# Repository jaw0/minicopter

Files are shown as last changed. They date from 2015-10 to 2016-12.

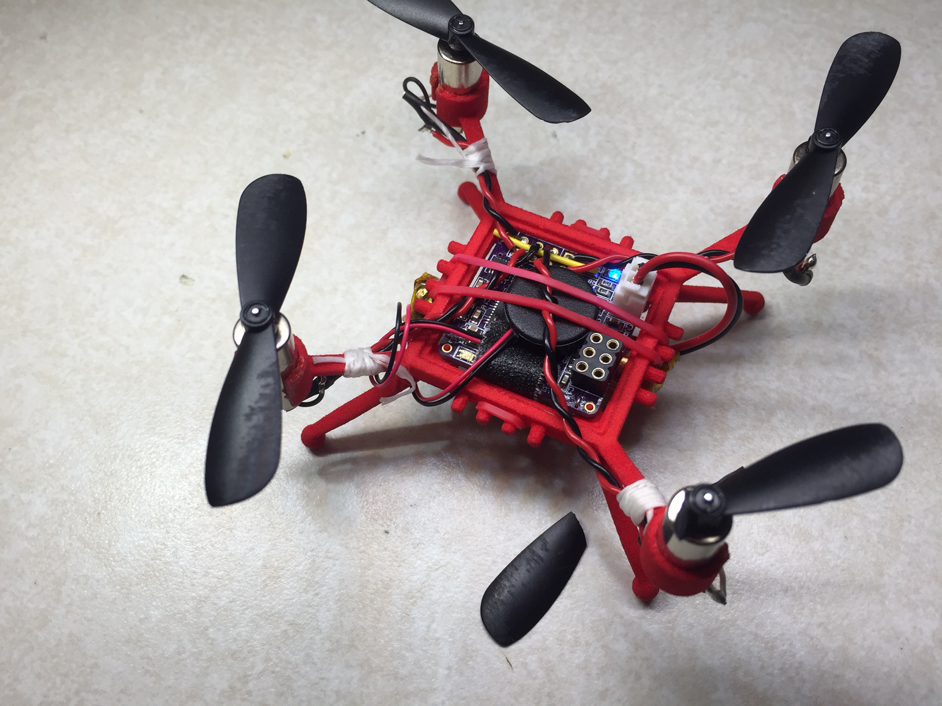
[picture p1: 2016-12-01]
img/IMG_0938.JPG

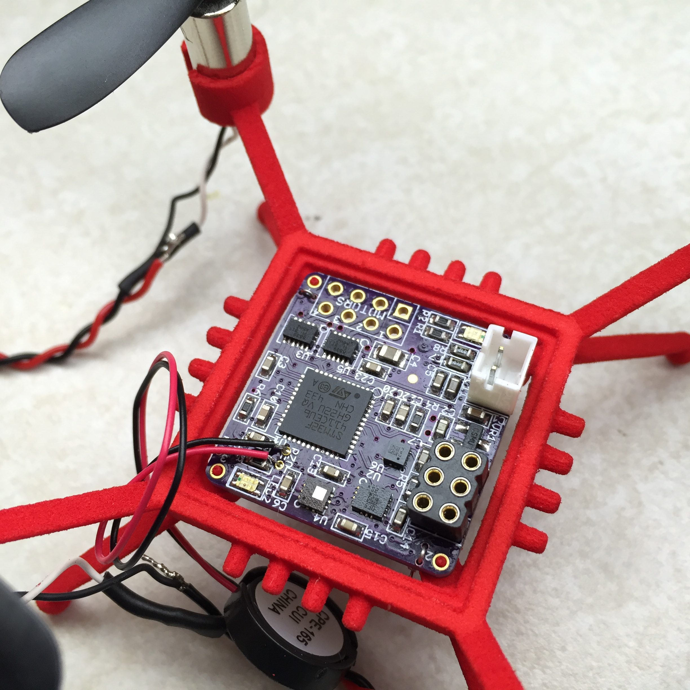
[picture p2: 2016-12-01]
img/IMG_0904.JPG

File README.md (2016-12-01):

teeny-tiny autonomous quadcopter flying machine

* 25mm square (smaller than one inch!)

* STM32F4 - ARM Cortex-M4

* 10 DOF IMU
  * accelerometer
  * gyro
  * magnetometer
  * barometer

* 3D printed frame

* buggy, poorly performing software

* see also: [hackaday.io](https://hackaday.io/project/7947-quadcopter-in-one-inch)

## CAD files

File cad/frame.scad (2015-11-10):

// Copyright (c) 2015
// Author: Jeff Weisberg <jaw @ tcp4me.com>
// Created: 2015-Oct-04 22:32 (EDT)
// Function: frame for mini-copter


show_env   = 0;

pcb_x      = 25.0;
pcb_y      = 25.0;
pcb_z      =  1.6;

peg_pos    = 1.25;	// in from corner
prop_x     = 56.0;	// prop diam plus margin
mot_z      = 10.0; 	// ht of center of motor
motor_phi  = 5.0;	// slight dihedral
motor_diam = 7;


//################################################################

mot_pos = (prop_x - pcb_x) / 2;
mot_armang = atan( (mot_z + 2) / (mot_pos + peg_pos) / sqrt(2) );

$fn = 64;
$fa = .5;
$fs = 0.05;

//################################################################

module vcyl(x,y,z,diam1, diam2, len){
    translate([x,y,z])
        cylinder(r1=diam1/2, r2=diam2/2, h=len);
}

module hcyl(x,y,z,diam1, diam2, len){
    translate([x,y,z])
        rotate([0,90,0])
            cylinder(r1=diam1/2, r2=diam2/2, h=len);
}

module box(x,y,z, dx,dy,dz){
    translate([x, y, z]) cube([dx, dy, dz]);
}


module proparm(){

    // board support+attach
    translate([ (pcb_x/2-peg_pos)*sqrt(2), 0, 0]) rotate([0,0,45]){
        vcyl(0,0,-4, 3.5, 3.5,4);
        // slightly tapered pins
        vcyl(0,0,-.1, 1.0, 0.85, 2.1);
        box(-3.5,-.5,-1.5, 4,1,1.5);
        box( -.5,-.5,-1.5, 1,4,1.5);

    }

    // legs
    translate([ (pcb_x/2-peg_pos)*sqrt(2), 0, -3.0]) rotate([0,30,0]){

        intersection(){
            union(){
                box(0,-1.5,2.0, 25, 3, 1);
                rotate([0,-3,0]) box(0,-.5,0, 25, 1, 3);
            }
            box(0,-1.5,-1, 25, 3, 4);
            hcyl(0,0,2.5, 5.3,2.25, 25);
        }
        translate([25,0,1.25]) sphere(2.0);
    }

    difference(){
        union(){
            // motor arms
            intersection(){
                translate([ (pcb_x/2-peg_pos)*sqrt(2), 0, -2.0]) rotate([0,-mot_armang,0]) {
                    box(0, -1.5, 0,   (mot_pos+peg_pos)*sqrt(2) / cos(mot_armang), 3.0,1 );
                    box(0,-.5,  -2, (mot_pos+peg_pos)*sqrt(2) / cos(mot_armang), 1,3.0 );
                }
                // clean up the bottom
                box(-5,-5,-4, 60,60,60);
            }
            // motor mounts
            translate([prop_x/2 * sqrt(2),0, mot_z]) rotate([0,-motor_phi,0]){
                vcyl(0,0,-3.5, motor_diam+2, motor_diam+2, 6.5 );

                // prop
                if( show_env ) color([.75,0,.75,1]) vcyl(0,0,5, 45, 45, 5);
            }

        }
        union(){
            // hole for motor
            translate([prop_x/2 * sqrt(2),0, mot_z]) rotate([0,-motor_phi,0]){
                vcyl(0,0,-5, motor_diam-.5, motor_diam-.5, 9 );
                rotate([0,0,90]) box(motor_diam/2-2, -.5,-5, 5,1,9);
            }
        }
    }
}

module cage(){
    // outer box
    difference(){
        union(){
            box( 28/2+.5, -28/2-2, -2.0, 2.0, 28+4, 4.0);
            box( 28/2-.5,  -28/2-2, -1.0, 2.0, 28+4, 2.0);
        }
        // clean up/bevel the corners
        union(){
            for(a = [-45, 45]){
                rotate([0,0,a])
                    translate([ (pcb_x/2-peg_pos)*sqrt(2), 0, 0])
                        rotate([0,-mot_armang,0])
                            box(-2,-4,-6.1,  8,8,2);
            }
        }
    }
    // rubber band attachment pegs
    hcyl(28/2+.5, -6, 0,  2,2,5);
    hcyl(28/2+.5,  6, 0,  2,2,5);
    hcyl(28/2+.5, -2, 0,  2,2,5);
    hcyl(28/2+.5,  2, 0,  2,2,5);

}


// ################################################################

if( show_env ) color([.75,0,.75, 1]) box(-pcb_x/2, -pcb_y/2, 0, pcb_x, pcb_y, pcb_z);

for( angle = [ 0 : 90 : 270 ] ){
    rotate([0,0,45+angle]) proparm();

    // outer cage
    rotate([0,0,angle]) translate([0,0,.4]) cage();

}

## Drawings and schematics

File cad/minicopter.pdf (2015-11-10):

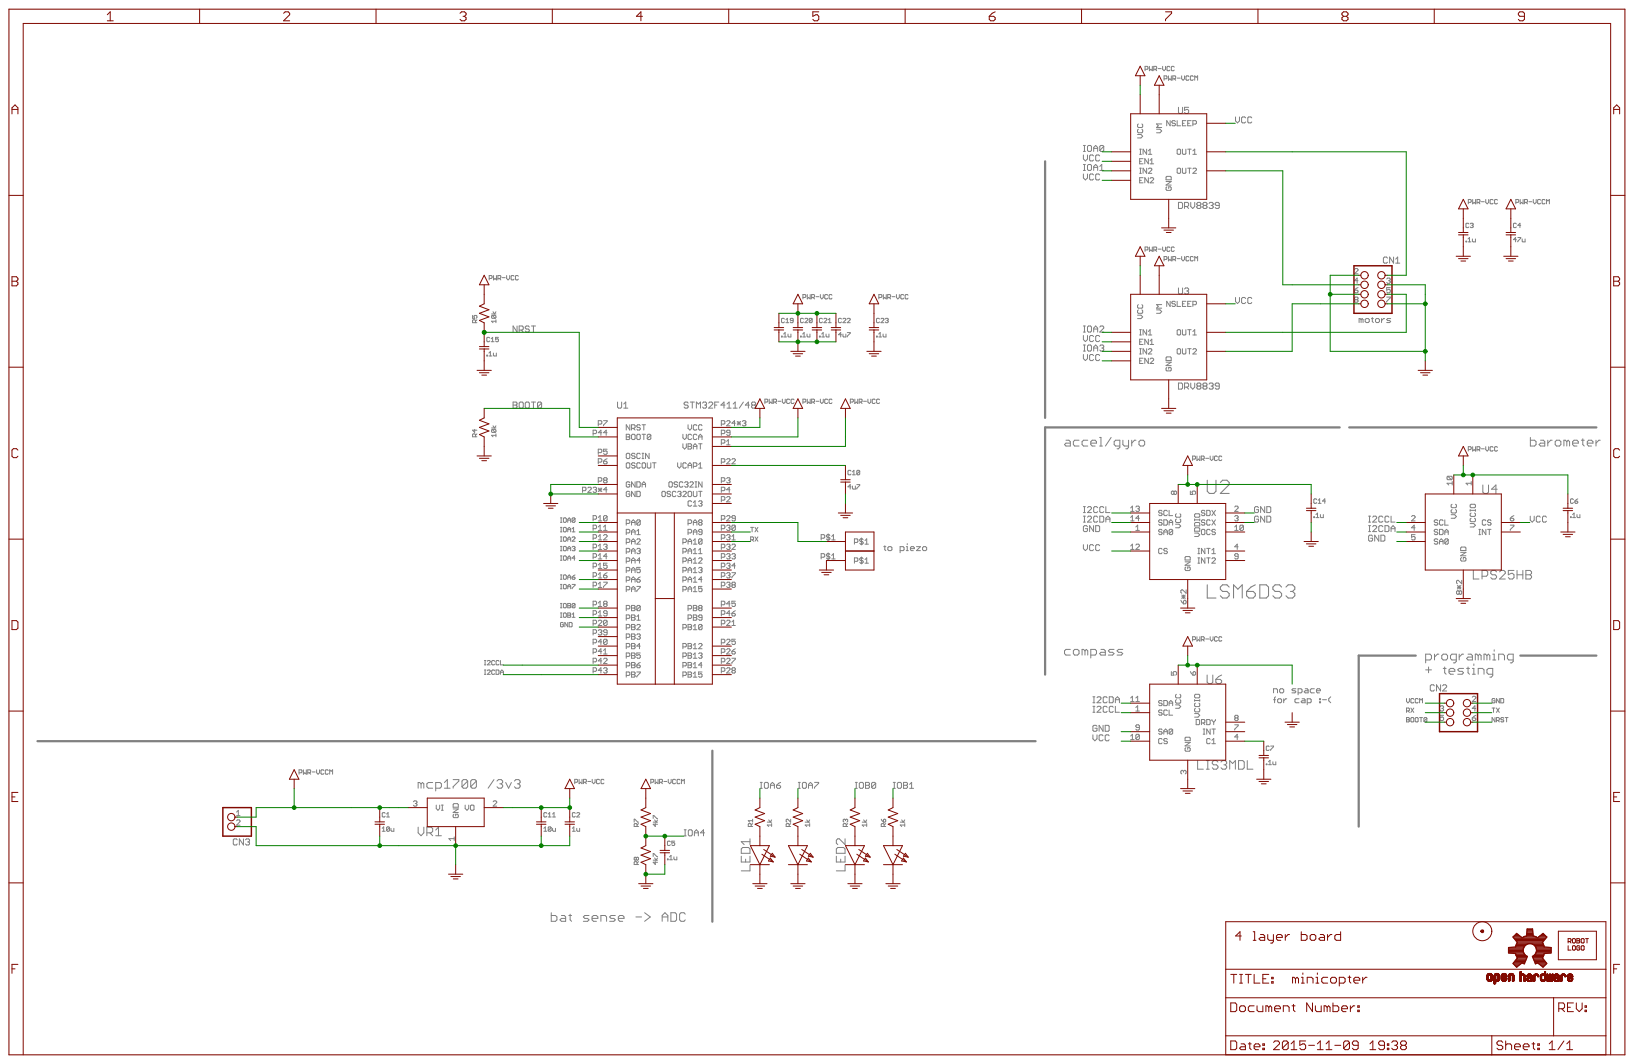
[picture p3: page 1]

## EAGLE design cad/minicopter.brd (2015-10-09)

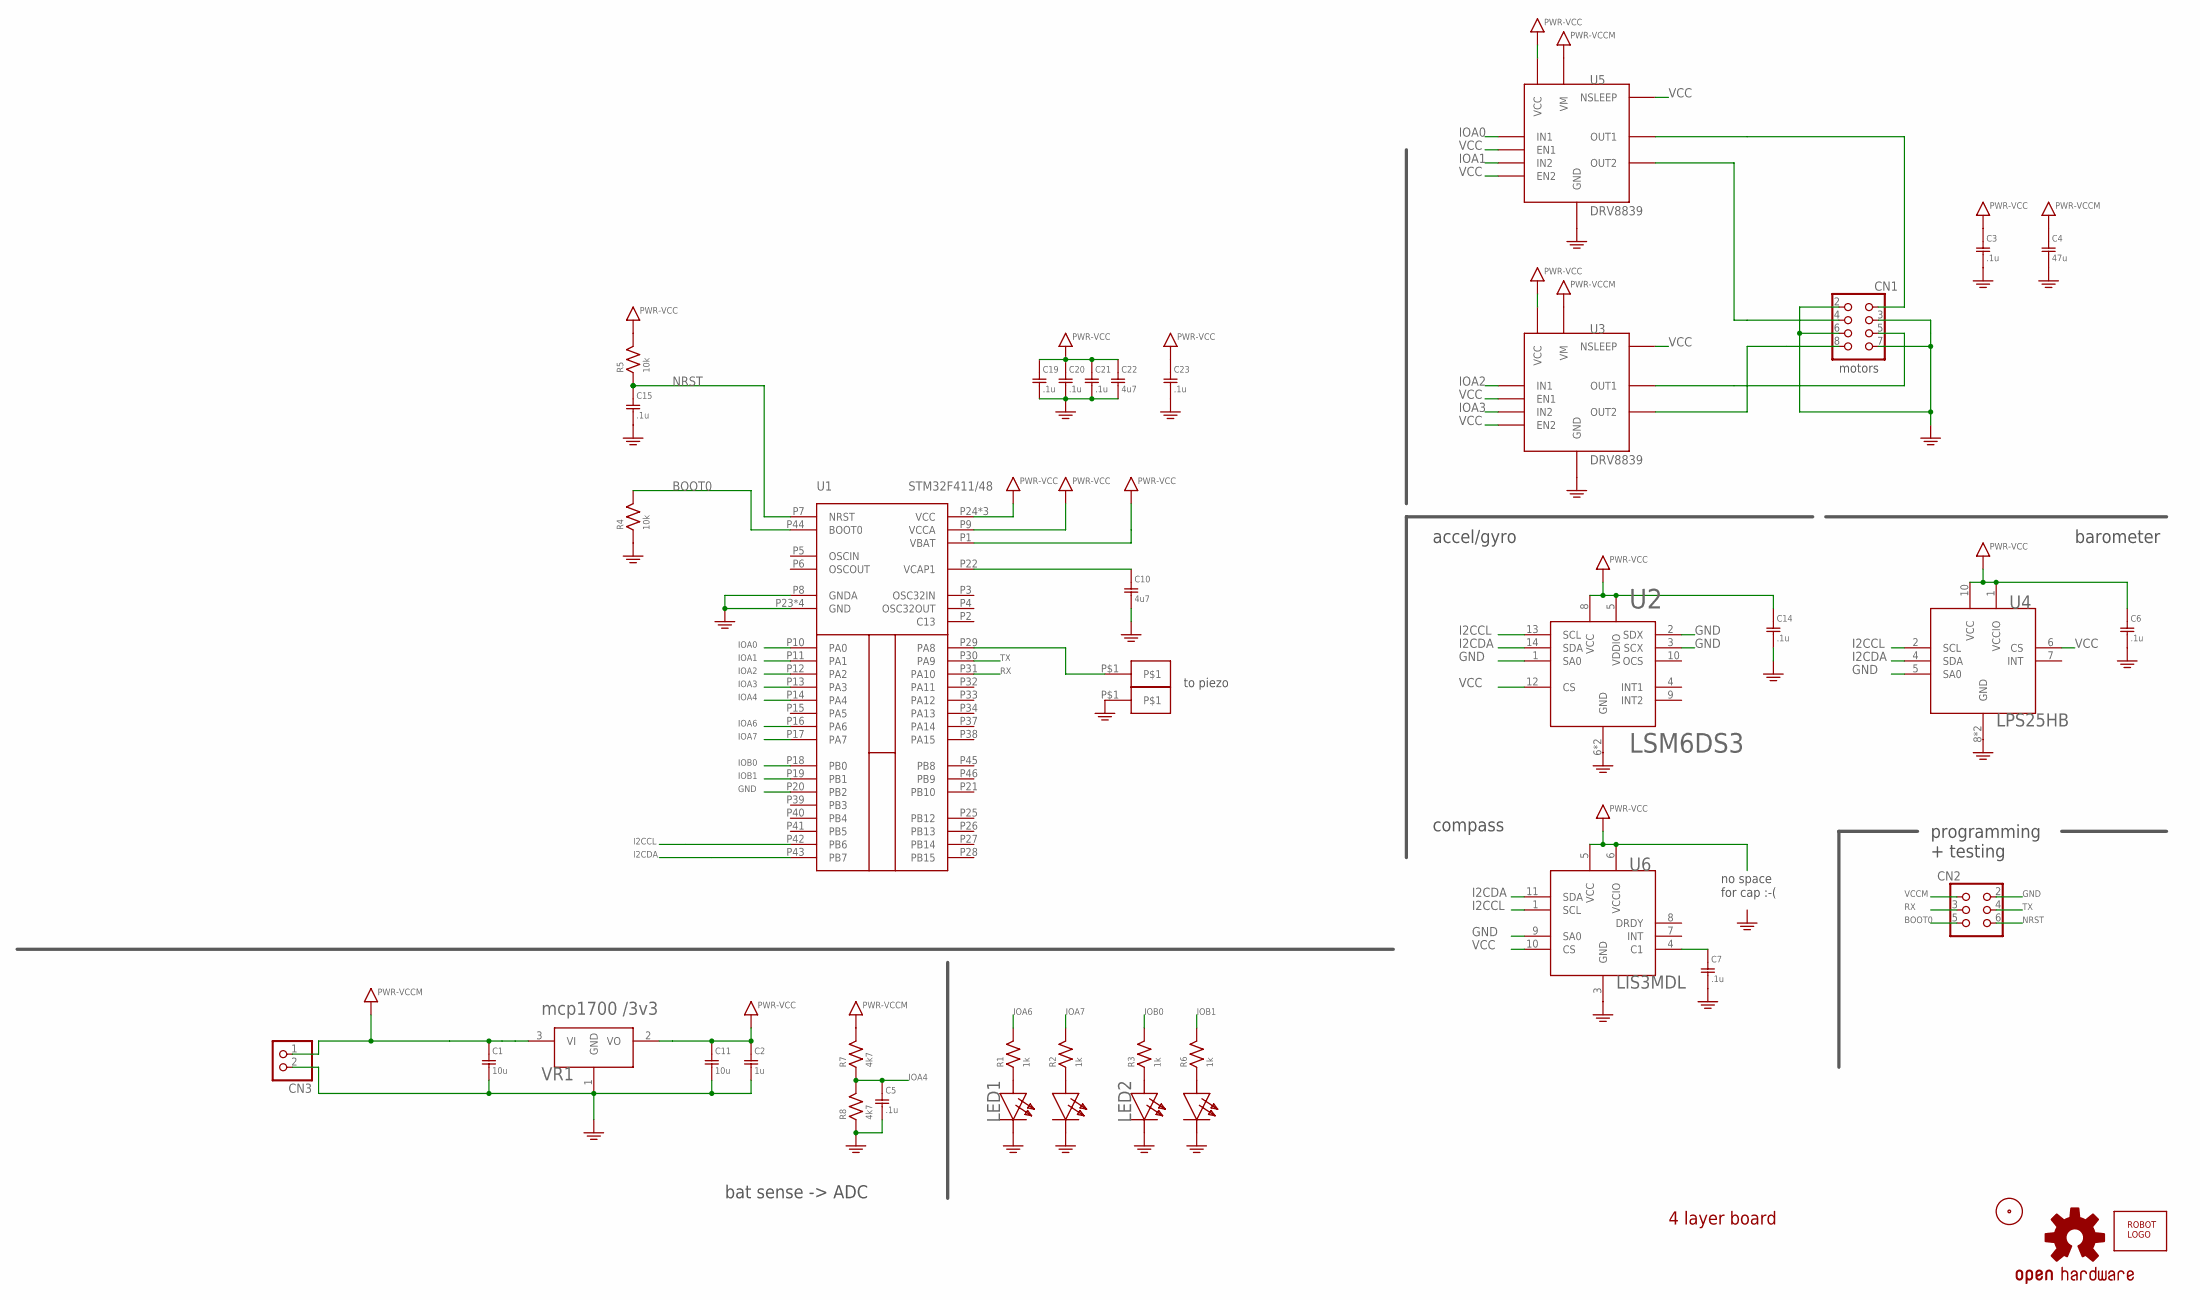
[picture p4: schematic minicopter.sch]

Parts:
C1, C11: 10u; SMD0603
C2: 1u; SMD0603
C3, C5, C6, C7, C14, C15, C19, C20, C21, C23: .1u; SMD0603
C4: 47u; SMD0805
C10, C22: 4u7; SMD0603
CN1: HEADER-2X4; HEADER-2X04-THM
CN2: HEADER-3X2-PTH
CN3: JST_2PIN-THM; JST-PH-2-THM
CN4, CN5: HEADER-1X1SMALL; HEADER-1X1-SMALL
LED1, LED2: LED-DUAL0805; SMD0805-DUAL
LOGO1: OSHW-LOGOM; OSHW-LOGO-M
R1, R2, R3, R6: 1k; SMD0603
R4, R5: 10k; SMD0603
R7, R8: 4k7; SMD0603
U1: STM32F411/48; UQPFN48
U2: LSM6DS3; LGA14A
U3, U5: DRV8839; WSON12
U4: LPS25HB; HLGA10L
U6: LIS3MDL; LGA12
U$1: ROBOTMAN-LOGO
U$2: FIDUCIAL
VR1: mcp1700 /3v3; SOT-23-3

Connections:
BOOT0: CN2.5, R4.2, U1.P44 (BOOT0)
GND: C1.2, C2.2, C3.2, C4.2, C5.2, C6.2, C7.2, C10.2, C11.2, C14.2, C15.2, C19.2, C20.2, C21.2, C22.2, C23.2, CN1.2, CN1.3, CN1.6, CN1.7, CN2.2, CN3.2 (1), CN5.P$1, LED1.2 (CB), LED1.3 (CR), LED2.2 (CB), LED2.3 (CR), R4.1, R8.1, U1.P8 (GNDA), U1.P20 (PB2), U1.P23 (GND), U1.P35 (GND), U1.P47 (GND), U1.PAD (GND), U2.1 (SA0), U2.2 (SDX), U2.3 (SCX), U2.6 (GND), U2.7 (GND), U3.5 (GND), U3.6 (GND), U3.GND3 (GND), U3.GND4 (GND), U3.GND5 (GND), U3.GND6 (GND), U3.GND7 (GND), U4.5 (SA0), U4.8 (GND), U4.9 (GND), U5.5 (GND), U5.6 (GND), U5.GND3 (GND), U5.GND4 (GND), U5.GND5 (GND), U5.GND6 (GND), U5.GND7 (GND), U6.3 (GND), U6.9 (SA0), VR1.1 (GND)
I2CCL: U1.P42 (PB6), U2.13 (SCL), U4.2 (SCL), U6.1 (SCL)
I2CDA: U1.P43 (PB7), U2.14 (SDA), U4.4 (SDA), U6.11 (SDA)
IOA0: U1.P10 (PA0), U5.10 (IN1)
IOA1: U1.P11 (PA1), U5.8 (IN2)
IOA2: U1.P12 (PA2), U3.10 (IN1)
IOA3: U1.P13 (PA3), U3.8 (IN2)
IOA4: C5.1, R7.1, R8.2, U1.P14 (PA4)
IOA6: R1.2, U1.P16 (PA6)
IOA7: R2.2, U1.P17 (PA7)
IOB0: R3.2, U1.P18 (PB0)
IOB1: R6.2, U1.P19 (PB1)
unnamed: LED1.1 (AB), R1.1
unnamed: LED1.4 (AR), R2.1
unnamed: LED2.1 (AB), R3.1
unnamed: LED2.4 (AR), R6.1
unnamed: CN1.1, U5.3 (OUT1)
unnamed: CN1.4, U5.4 (OUT2)
unnamed: C10.1, U1.P22 (VCAP1)
unnamed: CN1.5, U3.3 (OUT1)
unnamed: CN1.8, U3.4 (OUT2)
unnamed: C7.1, U6.4 (C1)
NRST: C15.1, CN2.6, R5.1, U1.P7 (NRST)
PZ0: CN4.P$1, U1.P29 (PA8)
RX: CN2.3, U1.P31 (PA10)
TX: CN2.4, U1.P30 (PA9)
VCC: C2.1, C3.1, C6.1, C11.1, C14.1, C19.1, C20.1, C21.1, C22.1, C23.1, R5.2, U1.P1 (VBAT), U1.P9 (VCCA), U1.P24 (VCC), U1.P36 (VCC), U1.P48 (VCC), U2.5 (VDDIO), U2.8 (VCC), U2.12 (CS), U3.7 (EN2), U3.9 (EN1), U3.11 (NSLEEP), U3.12 (VCC), U4.1 (VCCIO), U4.6 (CS), U4.10 (VCC), U5.7 (EN2), U5.9 (EN1), U5.11 (NSLEEP), U5.12 (VCC), U6.5 (VCC), U6.6 (VCCIO), U6.10 (CS), VR1.2 (VO)
VCCM: C1.1, C4.1, CN2.1, CN3.1 (2), R7.2, U3.1 (VM), U3.2 (VM), U5.1 (VM), U5.2 (VM), VR1.3 (VI)

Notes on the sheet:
programming + testing
bat sense -> ADC
motors
to piezo
no space for cap :-(
accel/gyro
compass
barometer
4 layer board

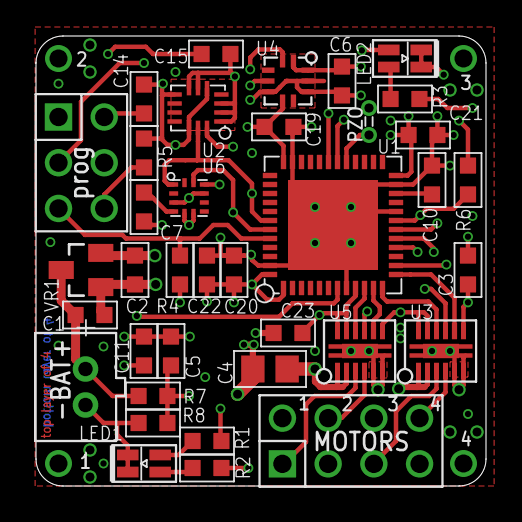
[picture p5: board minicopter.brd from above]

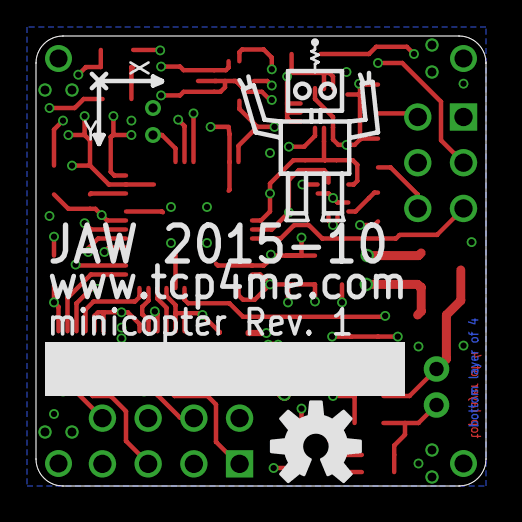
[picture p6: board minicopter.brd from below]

Board: 4 copper layers, 25.0 x 25.0 mm, 41 parts (2 on the bottom side), 29 nets.

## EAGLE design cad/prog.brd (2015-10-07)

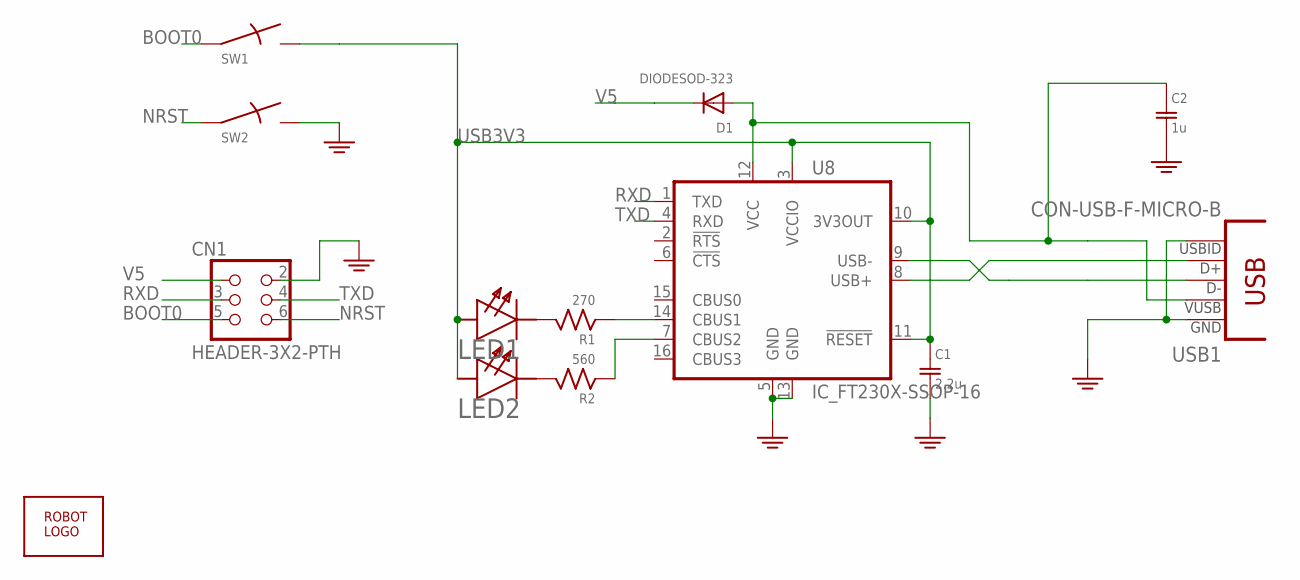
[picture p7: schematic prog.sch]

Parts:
C1: 2.2u; SMD0603
C2: 1u; SMD0603
CN1: HEADER-3X2-PTH
D1: DIODESOD-323; SOD-323
LED1: GREEN; SMD0603D
LED2: ORANGE; SMD0603D
R1: 270; SMD0603
R2: 560; SMD0603
SW1, SW2: SWITCHKMR211; KMR211
U8: IC_FT230X-SSOP-16; SSOP-16-FTDI
U$1: ROBOTMAN-LOGO
USB1: CON-USB-F-MICRO-B; CONN_USB_MICRO-B

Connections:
BOOT0: CN1.5, SW1.1, SW1.3
GND: C1.2, C2.2, CN1.2, SW2.2, SW2.4, U8.5 (GND), U8.13 (GND), USB1.P4 (USBID), USB1.P5 (GND)
unnamed: U8.8 (USB+), USB1.P3 (D+)
unnamed: U8.9 (USB-), USB1.P2 (D-)
unnamed: LED1.C, R1.2
unnamed: LED2.C, R2.2
unnamed: R1.1, U8.14 (CBUS1)
unnamed: R2.1, U8.7 (CBUS2)
NRST: CN1.6, SW2.1, SW2.3
RXD: CN1.3, U8.1 (TXD)
TXD: CN1.4, U8.4 (RXD)
USB3V3: C1.1, LED1.A, LED2.A, SW1.2, SW1.4, U8.3 (VCCIO), U8.10 (3V3OUT), U8.11 (!RESET)
V5: CN1.1, D1.C
VBUS: C2.1, D1.A, U8.12 (VCC), USB1.P1 (VUSB)

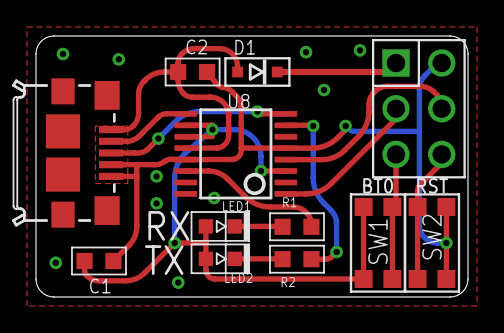
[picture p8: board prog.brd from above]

Board: 2 copper layers, 24.0 x 14.5 mm, 13 parts (1 on the bottom side), 14 nets.

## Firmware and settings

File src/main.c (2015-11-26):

/*
  Copyright (c) 2015
  Author: Jeff Weisberg <jaw @ tcp4me.com>
  Created: 2015-Oct-06 00:43 (EDT)
  Function: main

*/


#include <conf.h>
#include <proc.h>
#include <gpio.h>
#include <ioctl.h>
#include <error.h>
#include <stm32.h>
#include <userint.h>

#include "board.h"
#include "util.h"
#include "dazzle.h"


extern void blinky(void);


DEFUN(save, "save all config data")
{
    save_config("config.rc");
    return 0;
}

unsigned int
random(void){
    return lrand48();
}

void
onpanic(const char *msg){
    int i;

    set_motors(0,0,0,0);

    set_blinky( BLINK_OVERRIDE );
    set_leds_rgb(  0xFF0000, 0xFF0000 );
    beep_set(200, 127);

    splhigh();
    currproc = 0;

    while(1){
        set_leds_rgb(  0xFF0000, 0 );
        beep_set(150, 127);
        for(i=0; i<5000000; i++){ asm("nop"); }

        set_leds_rgb(  0, 0xFF0000 );
        beep_set(250, 127);
        for(i=0; i<5000000; i++){ asm("nop"); }
    }
}



//################################################################

void
main(void){

    board_init();
    set_led_1( 0xFF, 0xFF );
    set_led_2( 0xFF, 0xFF );

    run_script("config.rc");
    run_script("startup.rc");
    printf("\n");

    init_blinky();

    if( battery_voltage() <= BATT_WEAK ){
        set_blinky( BLINK_BATT_DEAD );
        play(16, "b-3b-3b-4b-4b-4b-3>b-3>>z");
        while(1) sleep(1);
    }

    play(8, "a>>4g4c+4");
    set_blinky( BLINK_WAIT_USER );

    // RSN - start flight interface

    // continue with interactive shell
}

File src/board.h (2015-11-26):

/*
  Copyright (c) 2015
  Author: Jeff Weisberg <jaw @ tcp4me.com>
  Created: 2015-Oct-06 00:34 (EDT)
  Function: board hardware config

*/

#define I2CUNIT			0

#define BATT_FULL 		2600	// "typical" reading for a full battery - ~ 2 * 4096 * 4.2V / 3.3V
#define BATT_WEAK		2172	// weak battery ~ 3.5V
#define BATT_DEAD      		1986	// dead battery ~ 3.2V

#define HWCF_GPIO_BATV		GPIO_A4
#define HWCF_ADC_BATV		ADC_1_4

#define HWCF_GPIO_AUDIO		GPIO_A8
#define HWCF_TIMER_AUDIO	TIMER_1_1

#define HWCF_GPIO_LED_1B	GPIO_B0
#define HWCF_GPIO_LED_1R	GPIO_B1
#define HWCF_GPIO_LED_2B	GPIO_A6
#define HWCF_GPIO_LED_2R	GPIO_A7

#define HWCF_TIMER_LED_1B	TIMER_3_3
#define HWCF_TIMER_LED_1R	TIMER_3_4
#define HWCF_TIMER_LED_2B	TIMER_3_1
#define HWCF_TIMER_LED_2R	TIMER_3_2

#define HWCF_GPIO_MOTOR_1	GPIO_A0
#define HWCF_GPIO_MOTOR_2	GPIO_A1
#define HWCF_GPIO_MOTOR_3	GPIO_A2
#define HWCF_GPIO_MOTOR_4	GPIO_A3

#define HWCF_TIMER_MOTOR_1	TIMER_2_1
#define HWCF_TIMER_MOTOR_2	TIMER_2_2
#define HWCF_TIMER_MOTOR_3	TIMER_2_3
#define HWCF_TIMER_MOTOR_4	TIMER_2_4

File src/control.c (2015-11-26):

/*
  Copyright (c) 2015
  Author: Jeff Weisberg <jaw @ tcp4me.com>
  Created: 2015-Sep-05 19:18 (EDT)
  Function: motor control

*/

#include <conf.h>
#include <nstdio.h>
#include <proc.h>
#include <userint.h>
#include <stm32.h>

#include "bot.h"
#include "util.h"
#include "dazzle.h"
#include "control.h"

#define GY2DEG		0.00007	// degrees/millisec
#define RADIAN2DEG  	57.2958
#define RADIAN2GYRO	(RADIAN2DEG / GY2DEG)
#define CIRCLE2GYRO	5142857
#define SEALEVEL	4150272		// 1013.25 * 4096
#define FA		15
#define FC		15
#define FP		15
#define AALPHA		24
#define CALPHA		24
#define PALPHA		100.0
#define VALPHA		200.0
#define ZALPHA		2047
#define AALPH2		((AALPHA+1) / 2)
#define CALPH2		((CALPHA+1) / 2)
#define ZALPH2		((ZALPHA+1) / 2)

#define MOTOR_AMAX	800

#define GYRO2DEG(x)	((x) * 7 / 100000)
#define DEG2GYRO(x)	((x) * 100000 / 7)


int   accx_lpf     = 0;
int   accy_lpf     = 0;
int   accz_lpf     = 1000;
int   magx_lpf     = 0;
int   magy_lpf     = 0;
int   magz_lpf     = 0;
int   press_lpf    = SEALEVEL;
int   angle_gp     = 0;
int   angle_gr     = 0;
int   angle_gy     = 0;
int   angle_ax     = 0;
int   angle_ay     = 0;
int   angle_mz     = 0;
int   angle_ez     = 0;
int   offset_yaw   = 0;
int   offset_az    = 1000;
int   offset_press = SEALEVEL;
int   baro_alt     = 0;
// positive pitch  = > nose up
// positive roll   = > right up
int   angle_pitch  = 0;
int   angle_roll   = 0;
int   angle_yaw    = 0;
float altitude     = 0;
float valtitude    = 0;
int   err_ip       = 0;
int   err_ir       = 0;
int   err_iy       = 0;

// desired set points
int target_pitch = 0;
int target_roll  = 0;
int target_yaw   = 0;
int target_gx    = 0;
int target_gy    = 0;
int target_gz    = 0;
int target_alt   = 0;
int target_valt  = 0;
// simple feedforward
int motor_ff     = 0;
int uhoh_count   = 0;
int moving	 = 0;

int err_p, err_r, err_y, err_a;
int adj_p, adj_r, adj_y, adj_a;

extern float  atan2f(float, float);
extern double atan2(double, double);


void
filter_reset(void){

    accx_lpf    = 0;
    accy_lpf    = 0;
    accz_lpf    = 1000;
    magx_lpf    = 0;
    magy_lpf    = 0;
    magz_lpf    = 0;
    press_lpf   = SEALEVEL;
    angle_gp    = 0;
    angle_gr    = 0;
    angle_gy    = 0;
    angle_pitch = 0;
    angle_roll  = 0;
    angle_yaw   = 0;
    offset_yaw  = 0;
    err_ip      = 0;
    err_ir      = 0;
    err_iy      = 0;
    altitude    = 0;
    valtitude   = 0;
    adj_p       = 0;
    adj_r       = 0;
    adj_y       = 0;
    adj_a       = 0;
    err_p       = 0;
    err_r       = 0;
    err_y       = 0;
    err_a       = 0;
    uhoh_count  = 0;
    moving      = 0;
}

void
acc_filter(void){
    // lpf
    accx_lpf  = (FA * accx_lpf + 256 * accel_x()) / (FA + 1);
    accy_lpf  = (FA * accy_lpf + 256 * accel_y()) / (FA + 1);
    accz_lpf  = (FA * accz_lpf + 256 * accel_z()) / (FA + 1);
}

void
mag_filter(void){
    // lpf
    magx_lpf  = (FC * magx_lpf + 256 * (compass_x() - MAG_OFF_X)) / (FC + 1);
    magy_lpf  = (FC * magy_lpf + 256 * (compass_y() - MAG_OFF_Y)) / (FC + 1);
    magz_lpf  = (FC * magz_lpf + 256 * (compass_z() - MAG_OFF_Z)) / (FC + 1);
}

void
press_filter(void){

    press_lpf = (FP * press_lpf + current_pressure()) / (FP + 1);
}


void
filter_sensors(void){

    acc_filter();
    mag_filter();
    press_filter();

    // angles reported by accelerometer
    angle_ax  = - atan2f( (float)accx_lpf, (float)accz_lpf) * RADIAN2GYRO;
    angle_ay  =   atan2f( (float)accy_lpf, (float)accz_lpf) * RADIAN2GYRO;
    angle_mz  =   atan2f( (float)magx_lpf, (float)magy_lpf) * RADIAN2GYRO;

    // bias yaw angle around target, to avoid handling the discontinuity going through the filter
    angle_ez =    angle_mz - target_yaw - offset_yaw;
    angle_ez =    (angle_ez + 2 * CIRCLE2GYRO) % CIRCLE2GYRO;
    if( angle_ez > CIRCLE2GYRO/2) angle_ez = CIRCLE2GYRO - angle_ez;

    // informational only
    angle_gr  += gyro_x();
    angle_gp  += gyro_y();
    angle_gy  += gyro_z();

    // my, what nice math you have.
    // you have such a lovely file.
    // -- complimentary filter
    angle_pitch += gyro_y();
    angle_roll  += gyro_x();
    angle_yaw   += gyro_z();

    // complementary filter
    angle_pitch = (AALPHA * angle_pitch + angle_ax + AALPH2) / (AALPHA+1);
    angle_roll  = (AALPHA * angle_roll  + angle_ay + AALPH2) / (AALPHA+1);
    // RSN - improve compass calibration and uncomment
    // angle_yaw   = (CALPHA * angle_yaw   + angle_ez + CALPH2) / (CALPHA+1);
#if 0
    // altitude (units of um)
    //     meters = (1-(Pressure/1013.25)^0.190284) * 44307
    //            ~ - reading * 0.190284 * 44307 / 4096 / 1013.25
    baro_alt    = (offset_press - press_lpf) * 2031;

    int prevalt  = altitude;
    int prevvalt = valtitude;
    valtitude  += (accz_lpf - offset_az) / 256;
    altitude   += valtitude * 0.0098;	// um; 9.8/1000

    altitude    = (PALPHA * altitude   + baro_alt) / (PALPHA+1);
    valtitude   = (VALPHA * valtitude  + 102.0 * (altitude - prevalt) ) / (VALPHA+1);
#endif
}

/****************************************************************/

void
read_all_sensors(void){
    read_imu_all();
    read_compass();
    read_pressure();
    read_battery();
}


void
reset_control(){
    int i;

    filter_reset();
    imu_calibrate();

    for(i=0; i<500; i++){
        read_all_sensors();
        acc_filter();
        mag_filter();
        press_filter();
        pause();
    }

    offset_yaw   = atan2f( (float)magx_lpf, (float)magy_lpf) * RADIAN2GYRO;
    offset_press = press_lpf;
    offset_az    = accz_lpf;
}

int
safety_check(void){

    int p = ABS(angle_pitch);
    int r = ABS(angle_roll);
    int y = ABS(gyro_z());

    if( p > DEG2GYRO(90) )  goto uhoh;
    if( r > DEG2GYRO(90) )  goto uhoh;
    if( y > DEG2GYRO(1)/5 ) goto uhoh;

    if( battery_voltage() < BATT_DEAD ) goto uhoh;

    uhoh_count = 0;
    return 0;

uhoh:
    if( ++uhoh_count > 100 ){
        return 1;
    }

    return 0;
}

static inline int
ibound(int v, int lim){

    //if( v > lim ) return lim;
    //if( v <-lim ) return -lim;
    return v;
}
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

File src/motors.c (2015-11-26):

/*
  Copyright (c) 2015
  Author: Jeff Weisberg <jaw @ tcp4me.com>
  Created: 2015-Oct-06 00:29 (EDT)
  Function: motors

*/

#include <conf.h>
#include <proc.h>
#include <gpio.h>
#include <pwm.h>
#include <ioctl.h>
#include <error.h>
#include <stm32.h>
#include <userint.h>

#include "board.h"


DEFVAR(short, motor_testspeed, 128, UV_TYPE_US | UV_TYPE_CONFIG, "motor test speed")

void
set_motors(int m1, int m2, int m3, int m4){
    int bv = battery_voltage();

    if( bv ){
        // adjust for battery voltage
        m1 = (m1 * BATT_FULL) / bv;
        m2 = (m2 * BATT_FULL) / bv;
        m3 = (m3 * BATT_FULL) / bv;
        m4 = (m4 * BATT_FULL) / bv;
    }

    if( m1 < 0 ) m1 = 0;
    if( m2 < 0 ) m2 = 0;
    if( m3 < 0 ) m3 = 0;
    if( m4 < 0 ) m4 = 0;

    if( m1 > 1023 ) m1 = 1023;
    if( m2 > 1023 ) m2 = 1023;
    if( m3 > 1023 ) m3 = 1023;
    if( m4 > 1023 ) m4 = 1023;

    pwm_set( HWCF_TIMER_MOTOR_1, m1 );
    pwm_set( HWCF_TIMER_MOTOR_2, m2 );
    pwm_set( HWCF_TIMER_MOTOR_3, m3 );
    pwm_set( HWCF_TIMER_MOTOR_4, m4 );

}

DEFUN(testmotors, "test motors")
{

    printf("M1\n");
    set_motors(motor_testspeed, 0, 0, 0);
    sleep(1);
    set_motors(0,0,0,0);
    sleep(1);

    printf("M2\n");
    set_motors(0, motor_testspeed, 0, 0);
    sleep(1);
    set_motors(0,0,0,0);
    sleep(1);

    printf("M3\n");
    set_motors(0, 0, motor_testspeed, 0);
    sleep(1);
    set_motors(0,0,0,0);
    sleep(1);

    printf("M4\n");
    set_motors(0, 0, 0, motor_testspeed);
    sleep(1);
    set_motors(0,0,0,0);
    sleep(1);

    return 0;
}


DEFUN(testmotors2, "test motors")
{

    int m = atoi(argv[1] );
    set_motors( m, m, m, m );
    sleep(5);
    set_motors(0,0,0,0);
    return 0;

}

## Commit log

2015-10-07 rough draft
    [minicopter.brd, minicopter.sch, prog.brd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]
2015-10-08 motor driver
    [minicopter.brd, minicopter.sch]
2015-10-08 add magnetometer
    [minicopter.brd, minicopter.sch]
2015-10-09 add piezo
    [minicopter.brd, minicopter.sch]
2015-11-10 sch -> pdf
    [minicopter.sch]
2015-11-10 thicken frame
    [frame.scad]
2015-11-10 add stl
2015-11-26 gerber files
    [minicopter.GBL, minicopter.GBO, minicopter.GBP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]

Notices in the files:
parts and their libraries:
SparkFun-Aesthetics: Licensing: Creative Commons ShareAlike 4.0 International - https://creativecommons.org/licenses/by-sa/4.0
